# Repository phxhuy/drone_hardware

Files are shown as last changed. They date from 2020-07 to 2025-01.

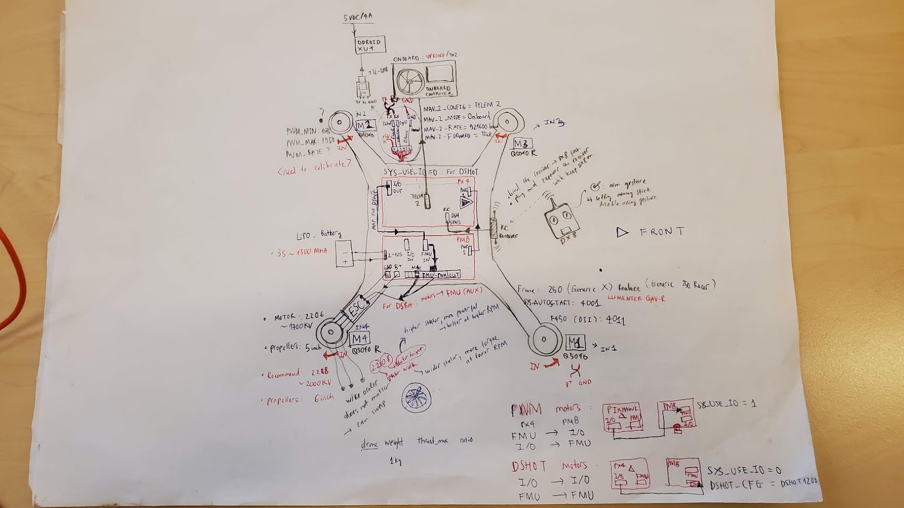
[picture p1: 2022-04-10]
wiring_diagrams_interfaces/huy_drone_diagrams.jpg

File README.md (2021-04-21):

# drone_hardware
A collection of hardware, drone design knowledge, and CAD models. It also includes basic software environment setup.

This page is a summary of basic quadrotor design for racing drones, commonly called FPV - First Person View - drones. The basic knowledge comes from various source, notably research groups like [uzh-rpg](https://github.com/uzh-rpg/rpg_quadrotor_control/wiki/RPG-Quadrotor-Setup), [ethz-asl](https://github.com/ethz-asl/mav_tools_public/wiki/Basic-MAV-Hardware), and dedicated communities and commercial pages like [getfpv.com](https://www.getfpv.com/learn/new-to-fpv-beginner/)

## Basic system design

*Drone Frame*
The most popular configuration for drone racing is 250 mm frame (hence, in the class of "mini" drones). Due to being light weight and durability, most drone frames are cut from carbon sheets, but note that carbon fiber is electrically conductive.

*Motor and propellers*
High-power motors with short propellers are selected. Typically the motor has around 2000 KV, and 5-inch propellers. However, longer propellers (e.g. 6") can also be used to provide extra payload for the drone to carry more sensors/computing units.

The recent protocol DShot for motor ESCs offers attractive [advantages](https://docs.px4.io/master/en/peripherals/dshot.html), such as reduced latency and better noise resistant, but particular details in wiring must be paid attention to, such as [this px4 guide](https://docs.px4.io/v1.9.0/en/assembly/quick_start_pixhawk4.html)

This [site](https://www.miniquadtestbench.com/motors/) provides a very good benchmark to compare the performance of different motors.

Generally,the larger the prop (by either increasing diameter, or pitch or both), the more energy it takes to spin it. Therefore, larger propeller or higher pitch length (4.8 – 5.1) will increase the aircraft’s speed but also use more power. [How to choose the right propeller](https://oscarliang.com/choose-propellers-mini-quad/)

A good tip from Oscar Liang's page:

- 5″ props for 210mm frame, use 2300KV-2700KV motors
- 6″ props for 250mm+ frame, use 1900KV-2300KV motors

*Autopilot board*
Pixhawk's PX4-based hardware and flight stack are selected due to its popularity and supports for autonomous flight. A good comparison between different open-source autopilot can be found in [this](https://dojofordrones.com/open-source-drone/)

*Computing Unit*
For main onboard computers, people usually using small, low-power computers such as [Intel Up Board](https://up-board.org/) (that has comparable performance as an [Intel Aero drone](https://click.intel.com/intel-aero-ready-to-fly-drone-2901.html)) or [Odroid XU4](https://www.hardkernel.com/shop/odroid-xu4-special-price/). Some also use a whole development kits such as [Qualcomm® Flight Pro™ Development Kit](https://www.intrinsyc.com/qualcomm-flight-pro-development-kit/)

## Weights

Normally racing drone is optimized so that it has minimum weight. Autonomous drones, however, require a bit more payload for additional processing computer(s), camera(s) and other sensor(s). The racing drone of [uzh-rpg], winner of IROS 2018 Drone Racing Event, has overall weight of around 900 g.

## Sensor suite

## Wiring diagrams for a PX4 drone

# Software Environment Setup

## Configure TX2 + Orbitty carrier board

Follow this detailed [instruction](https://magiccvs.byu.edu/wiki/#!computers/jetson.md) to setup the OS + support BSP for the combination through Jetpack Manager. Please note that even the instruction contains tiny mistakes.

Aslo follow this [instruction](https://magiccvs.byu.edu/wiki/#!computers/headless.md) to enable/disable headless mode for the TX2.

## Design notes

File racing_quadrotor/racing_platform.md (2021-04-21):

# AiR Lab basic racing drone design (version 2.0 rev. 01 - May 2020)

## Basic Components

- a Frame 250 mm, can afford up to 6-inch propellers
- Holybro Pixhawk 4 module + Power management board (PMB)
- Emax motors + ESC + Propellers
- Mounts, cables, ...

## Battery
- 3S Battery

## Cameras
- RGB Camera: FLIR Blackfly
- Odometry: Intel Tracker T265

## Computation Units

- Main computer: TX2 + Obitty Carrier Board (support 1 USB 3.0, 1 USB 2.0 OTG, and UART connections for Pixhawk module on extension port)
- Main computer: TX2 + Auvidea Carrier Board (support 2 USB 3.0, 1 USB 2.0 OTG, and extension port)

## Weights:

Base drone + RGB Camera + TX2 + Obitty Carrier Board: 700 g

- Base drone + RGB Camera: 533 g
- TX2 + Obitty Carrier Board: 195 g

3S Battery 2200: 180 g (3S Battery: 341 g)

Intel Tracker T265: 55 g

Intended solution total weight: 1129 g.

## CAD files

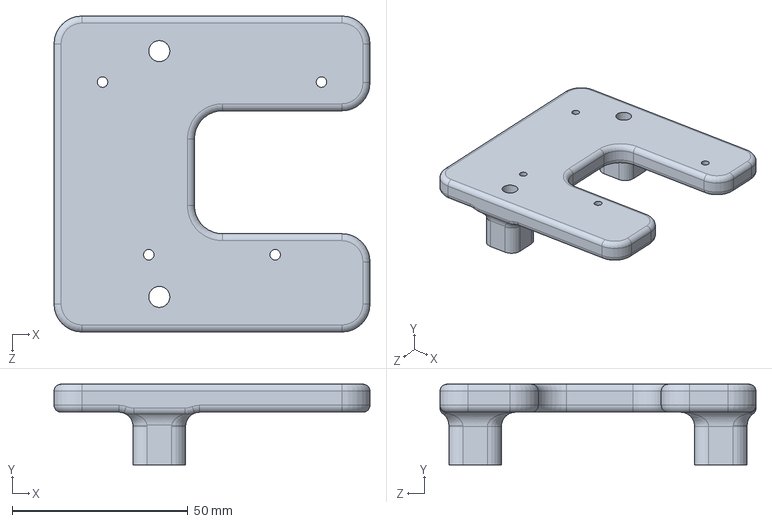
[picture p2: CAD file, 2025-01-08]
inspection_quadrotor/Lark/CAD/Lidar_gimbal_connector.SLDPRT
90.0 x 23.0 x 90.0 mm

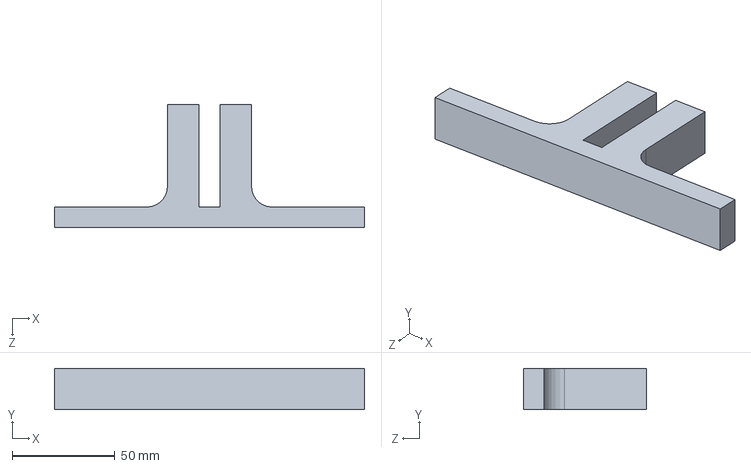
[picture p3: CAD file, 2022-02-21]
racing_quadrotor/CAD/general/april_tag_holder.SLDPRT
151.0 x 20.0 x 60.0 mm

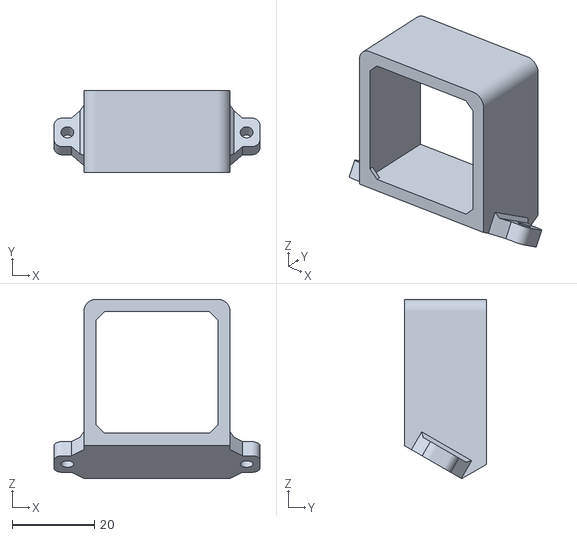
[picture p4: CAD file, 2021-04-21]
racing_quadrotor/CAD/racer_hybrid_ver3.0/Camera_Flir_BlackFly_S_BFS_U3_28S5M_C_mount v5.stl
50.0 x 20.0 x 43.5

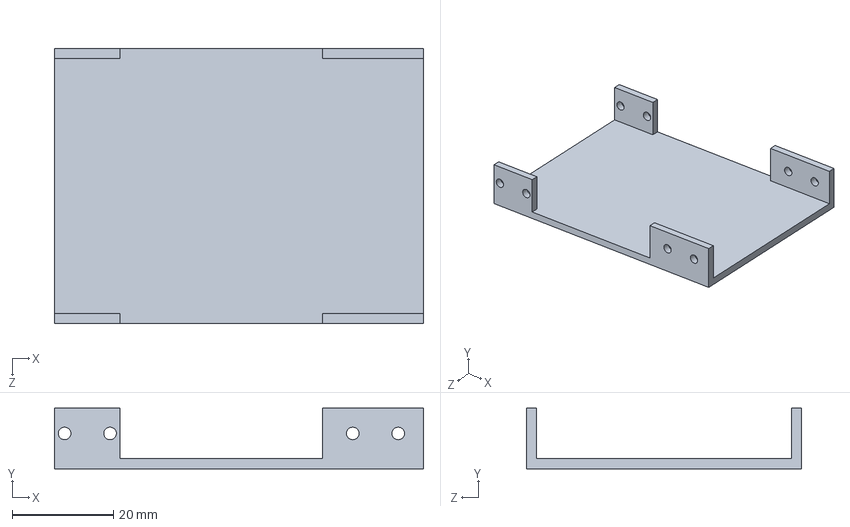
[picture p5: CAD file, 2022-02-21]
racing_quadrotor/CAD/racer_ver2.1/Autopilot_Plate_1_RV4.SLDPRT
73.0 x 12.0 x 54.5 mm

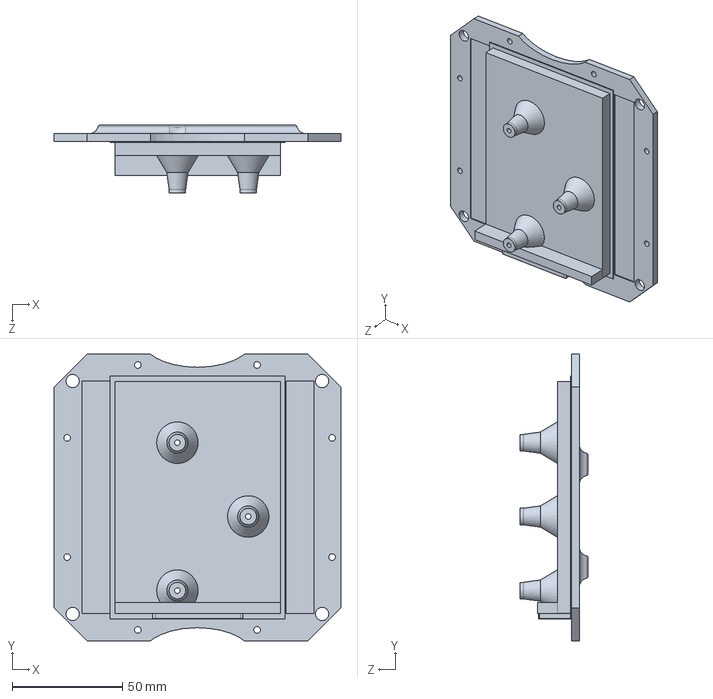
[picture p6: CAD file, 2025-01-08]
inspection_quadrotor/Lark/CAD/ORIN_MOUNT_3.0.f3d v1.SLDPRT
130.0 x 130.0 x 31.0 mm

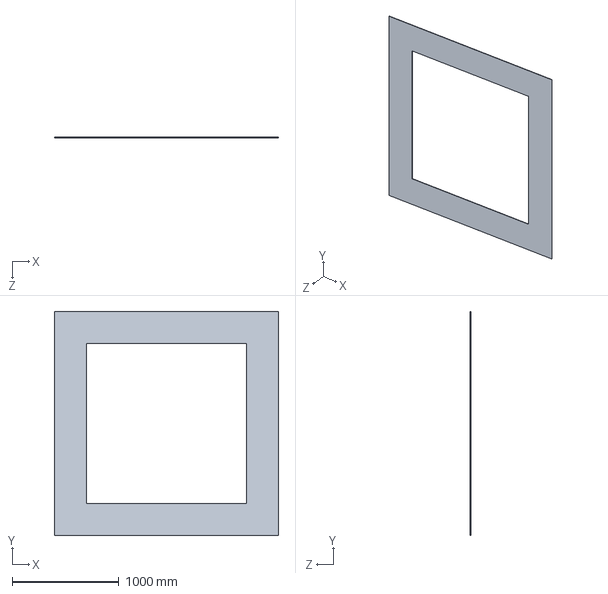
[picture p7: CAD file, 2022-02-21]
racing_quadrotor/CAD/general/gate_racing_2.1m_outer_1.5m_inner.SLDPRT
2100.0 x 2100.0 x 5.00 mm

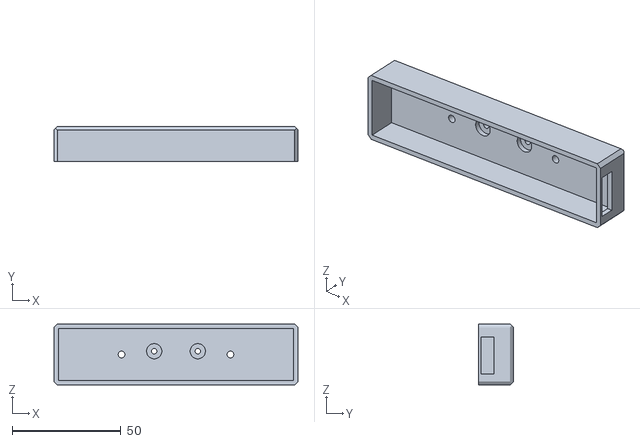
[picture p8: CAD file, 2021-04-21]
racing_quadrotor/CAD/racer_hybrid_ver3.0/T265_Cover_Mount_RV3_F360 v3.stl
112.0 x 16.0 x 28.0

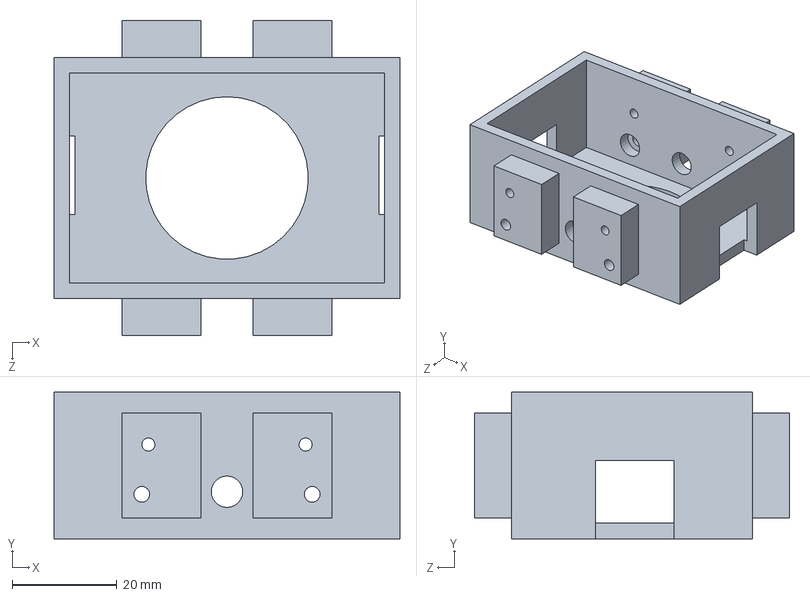
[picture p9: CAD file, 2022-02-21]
racing_quadrotor/CAD/racer_ver2.1/Event_Mount.SLDPRT
66.0 x 28.0 x 60.0 mm

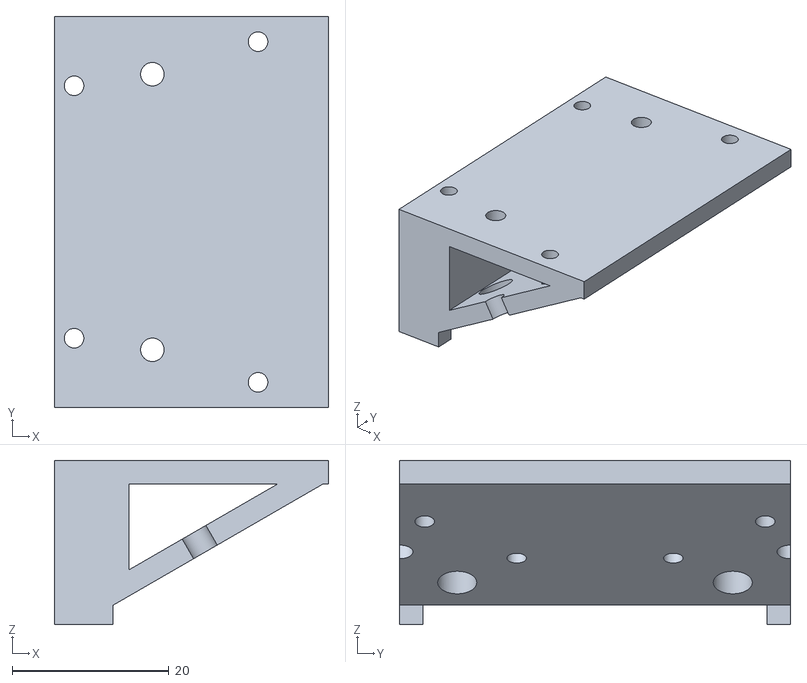
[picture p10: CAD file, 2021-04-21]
racing_quadrotor/CAD/racer_hybrid_ver3.0/T265_Mount_RV3_F360 v5.stl
35.0 x 50.0 x 21.0

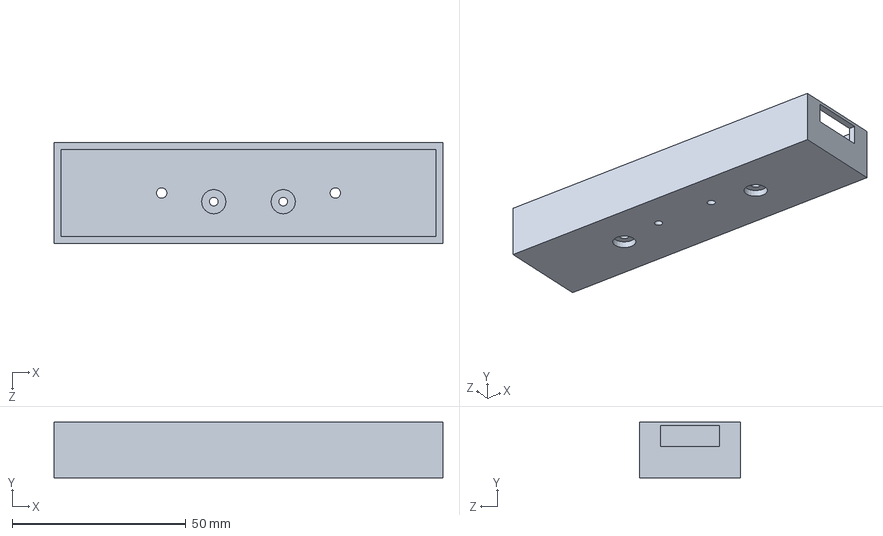
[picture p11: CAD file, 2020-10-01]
racing_quadrotor/CAD/racer_hybrid_ver3.0/T265_Cover_Mount_RV3.SLDPRT
112.0 x 16.0 x 29.0 mm

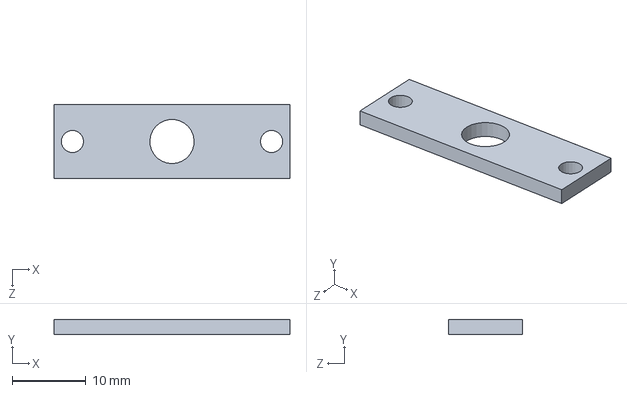
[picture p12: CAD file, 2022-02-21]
racing_quadrotor/CAD/racer_ver2.1/antennas_back_mount.SLDPRT
32.0 x 2.00 x 10.0 mm

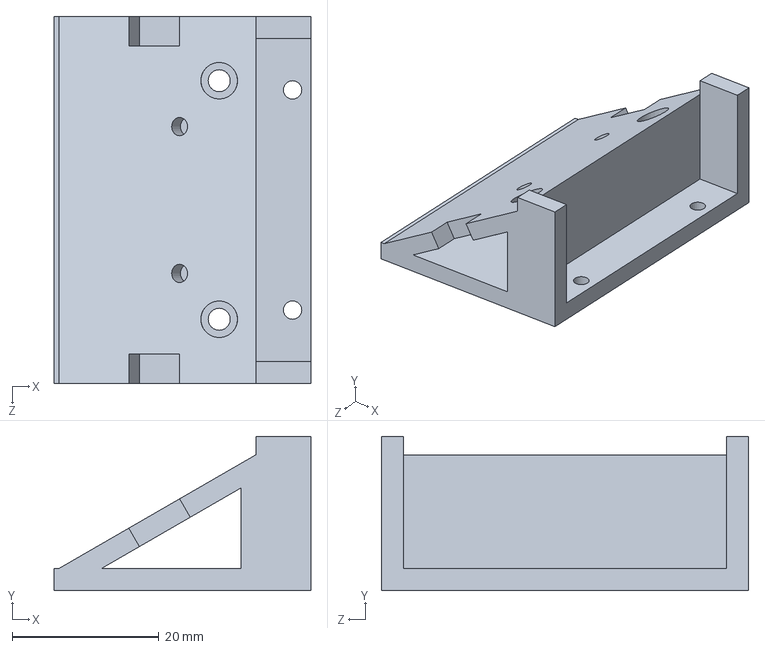
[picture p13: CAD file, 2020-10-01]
racing_quadrotor/CAD/racer_hybrid_ver3.0/T265_Mount_RV3.SLDPRT
35.0 x 21.0 x 50.0 mm

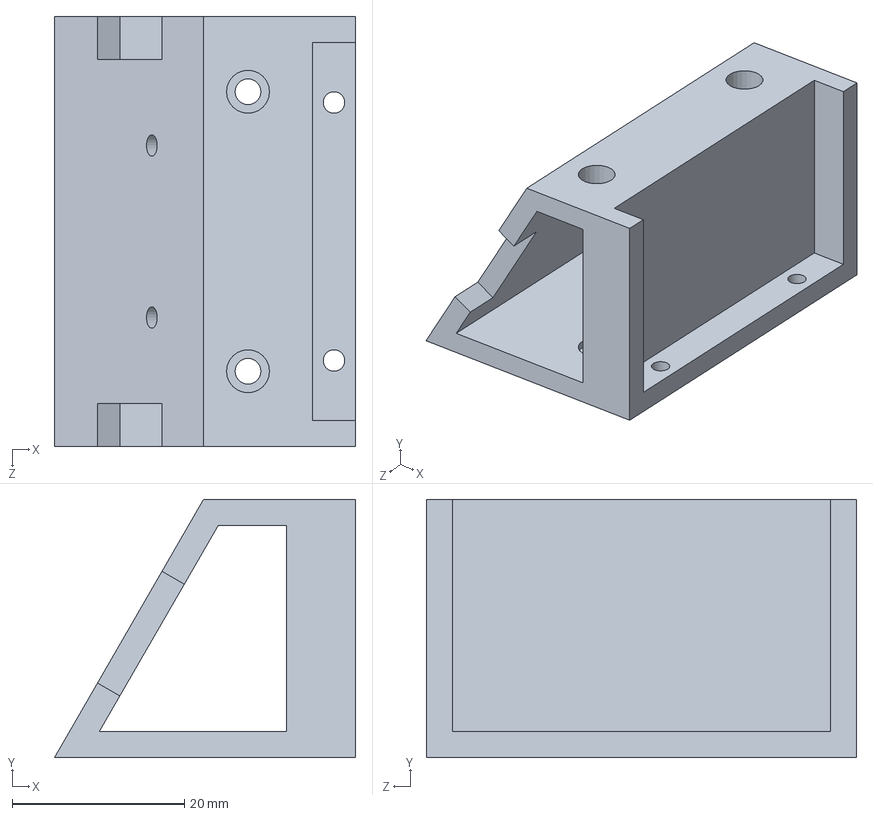
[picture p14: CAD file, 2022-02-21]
racing_quadrotor/CAD/racer_ver2.1/T265_Cover_Mount_RV4.SLDPRT
35.0 x 30.0 x 50.0 mm

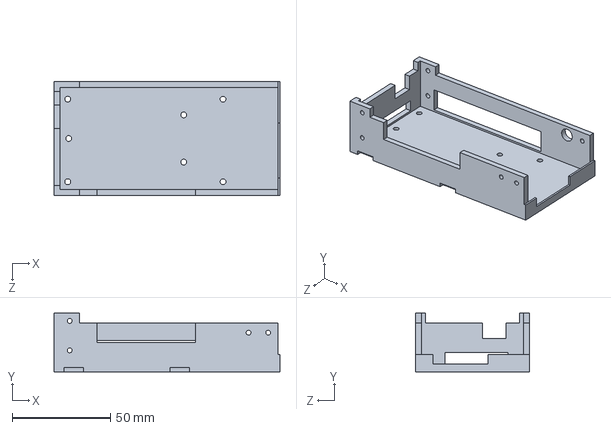
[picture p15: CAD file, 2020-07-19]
racing_quadrotor/CAD/racer_hybrid_ver3.0/TX2_Auvidea_Mount.SLDPRT
115.0 x 30.0 x 58.0 mm

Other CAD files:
racing_quadrotor/CAD/racer_ver2.1/Autopilot_Plate_1.SLDPRT
racing_quadrotor/CAD/racer_ver2.1/antennas_front_mount.SLDPRT
racing_quadrotor/CAD/racer_hybrid_ver3.0/All_Autopilot_Mount.SLDPRT
racing_quadrotor/CAD/racer_ver2.1/antennas_front.STL
racing_quadrotor/CAD/general/april_tag_holder.STL
racing_quadrotor/CAD/general/gate_racing_2.1m_outer_1.5m_inner.STL
racing_quadrotor/CAD/racer_hybrid_ver3.0/All_Autopilot_Mount.STL
racing_quadrotor/CAD/racer_hybrid_ver3.0/T265_Cover_Mount_RV3.STL
racing_quadrotor/CAD/racer_hybrid_ver3.0/T265_Mount_RV3.STL
racing_quadrotor/CAD/racer_hybrid_ver3.0/TX2_Auvidea_Mount.STL
racing_quadrotor/CAD/racer_ver1.2/CamMount.SLDPRT
racing_quadrotor/CAD/racer_ver1.2/TX2Mount.SLDPRT
racing_quadrotor/CAD/racer_ver1.2/TX2Mount.STL
racing_quadrotor/CAD/racer_ver2.0/CameraFLIRBlackFly_BFS_U3_28S5M_C.SLDPRT
racing_quadrotor/CAD/racer_ver2.0/PMBHanger.SLDPRT
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

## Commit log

2020-02-27 update wiki and add frame cad
2020-05-05 improved racer design version 1.2 to afford camera and TX2
    [CamMount.SLDPRT, CameraFLIRBlackFly_BFS_U3_28S5M_C.SLDPRT, TX2Mount.SLDPRT]
2020-05-06 New racer design version 2.0 CAD
    [CameraFLIRBlackFly_BFS_U3_28S5M_C.SLDPRT, PMBHanger.SLDPRT, PMBHanger.STL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]
2020-05-08 add PMB cover plate & fix PX4 Mount
    [PMB_Plate_battery.SLDPRT, PMB_Plate_battery.STL, PX4_Mount_RV2.SLDPRT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]
2020-05-11 design version 2.1 autopillot in one place
    [All_Autopilot_Mount.SLDPRT, All_Autopilot_Mount.STL, T265_Mount_RV3.SLDPRT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]
2020-05-12 fix T265 Mount for version 2.1
    [T265_Mount_RV3.SLDPRT, T265_Mount_RV3.STL]
2020-05-12 add antennas mount
    [antennas.SLDPRT, antennas.STL]
2020-05-14 add leg design for drone design v2 and fix plates errors
    [Autopilot_Plate_1.SLDPRT, Autopilot_Plate_1.STL, Autopilot_Plate_2.SLDPRT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]
2020-05-17 multiple fix for enlarged case for PX4 module
    [All_Autopilot_Mount.SLDPRT, All_Autopilot_Mount.STL, Autopilot_Plate_1.SLDPRT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]
2020-05-26 add blackfly cam mount
    [BFS_Cam_Mount_RV3.SLDPRT, BFS_Cam_Mount_RV3.STL]
2020-06-28 add T265 cover
    [T265_Cover_Mount_RV3.SLDPRT, T265_Cover_Mount_RV3.STL]
2020-07-17 add design for Anna class
    [All_Autopilot_Mount.SLDPRT, All_Autopilot_Mount.STL]
2020-07-18 add Auvidea TX2 board mount
    [TX2_Auvidea_Mount.SLDPRT, TX2_Auvidea_Mount.STL]
2020-07-19 adjustments for tx2 frame
    [TX2_Auvidea_Mount.SLDPRT, TX2_Auvidea_Mount.STL]
2020-08-24 add thicker case for TX2 (ver 2.0, ver 2.1)
    [TX2Inside_Mount.SLDPRT, TX2Inside_Mount.STL]
2020-08-25 fix base mount design for ver 2.1
    [All_Autopilot_Mount.SLDPRT, All_Autopilot_Mount.STL, TX2Inside_Mount.SLDPRT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]
2020-10-01 fix T265 mount problem for Ida
    [T265_Cover_Mount_RV3.SLDPRT, T265_Cover_Mount_RV3.STL, T265_Mount_RV3.SLDPRT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]
2020-10-01 add T265 mount for Anna
    [T265_Cover_Mount_RV3.SLDPRT, T265_Cover_Mount_RV3.STL, T265_Mount_RV3.SLDPRT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]
2020-10-10 update README and add wiring interface
2020-10-10 add Oribtty UART connection
2021-04-21 add mounts for intel realsense D435i and T265
    [Camera_Flir_BlackFly_S_BFS_U3_28S5M_C_mount v5.stl, D435iMount.SLDPRT, D435iMount.STL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]
2021-06-04 add event based camera mount
    [Event_Mount.SLDPRT, Event_Mount.STL]
2021-06-17 fix event mount not fitting
    [Event_Mount.SLDPRT, Event_Mount.STL]
2022-02-21 Update various mounts for ida class
    [Autopilot_Plate_1.SLDPRT, Autopilot_Plate_1_RV4.SLDPRT, Autopilot_Plate_1_RV4.STL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]
2025-01-08 adding CAD files for inspection quadrotors
    adding cad files for
    - Orin AGX computer mount
    - Lidar gimbal connector
    [Lidar_gimbal_connector.SLDPRT, ORIN_MOUNT_3.0.f3d v1.SLDPRT]
